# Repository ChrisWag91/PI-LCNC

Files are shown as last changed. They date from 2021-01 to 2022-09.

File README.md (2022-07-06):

 
# PI-LCNC

*THIS REPOSITORY IS WORK IN PROGRESS*

An open source project to use a Raspberry Pi 4 as a CNC controller using LinuxCNC.

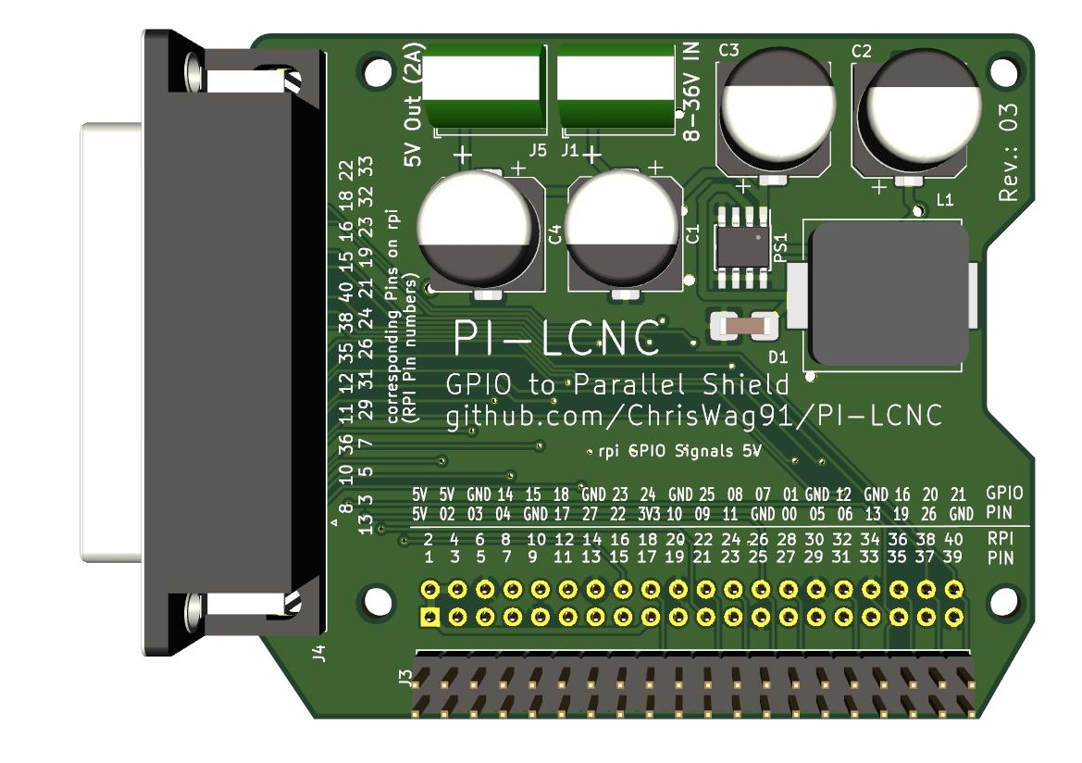
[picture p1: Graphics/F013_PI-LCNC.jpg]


You can find further information about the concept in this Youtube video:

<a href="https://youtu.be/qL530kJUmII
" target="_blank">Detailed Youtube Video</a>

It is designed to work combined with the [*RPI Levelshifter Hat*](https://github.com/ChrisWag91/rpi_level_shifter_hat) and a *CNC Breakout Board* with a parallel interface.

RPI 4 <==> [RPI Levelshifter Hat](https://github.com/ChrisWag91/rpi_level_shifter_hat) <==> PI-LCNC <==> [CNC-BOB (=Break out Board)](https://www.aliexpress.com/wholesale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)

*Concept:*

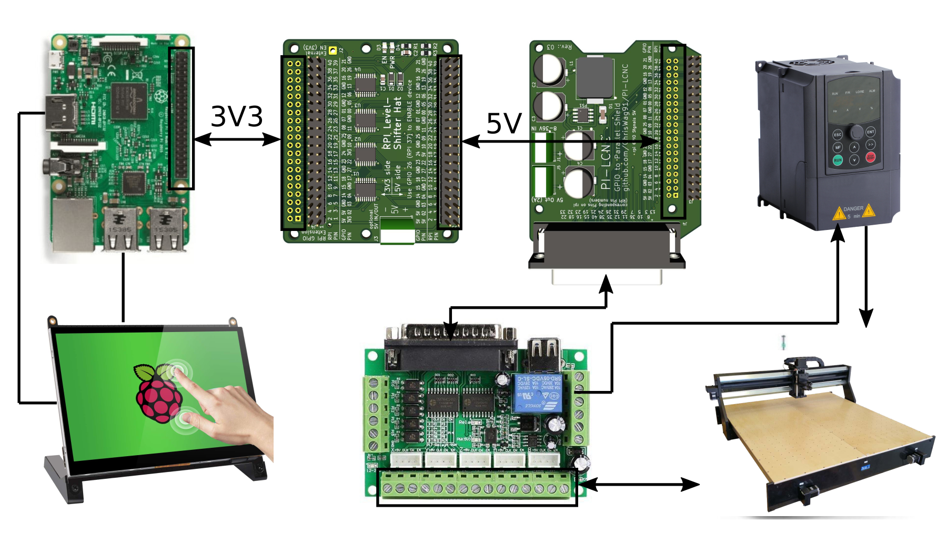
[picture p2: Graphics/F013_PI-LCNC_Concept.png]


This repository contains the manufacturing data for the PI-LCNC adapter PCB as well as configuration instructions and files for Linux CNC.

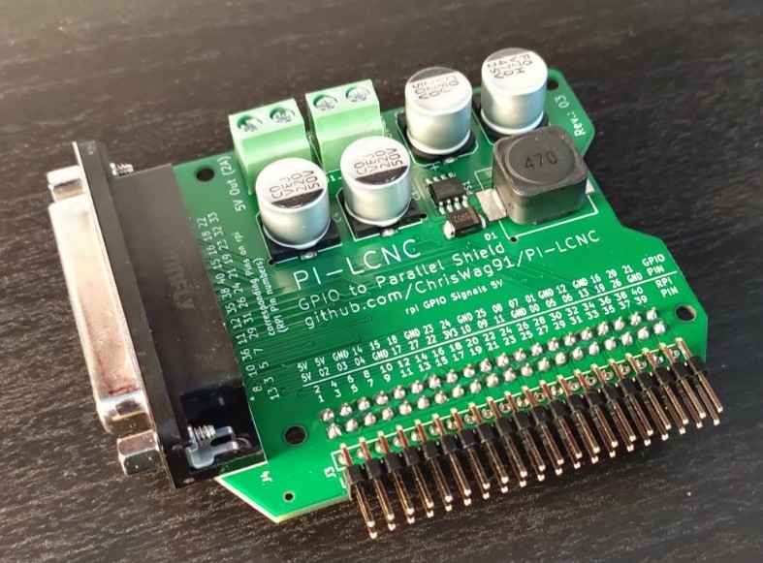
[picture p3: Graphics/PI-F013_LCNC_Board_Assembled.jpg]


Make sure to check the steps given under *Usage & Setup*

## Features
- DC-DC Power Supply for Raspberry Pi (Input Voltage 8-36V)
- Adapter for LPT connector
- Pin header for additional 5V signals from the Raspberry Pi

## Limitations
- 15000 Steps / s max due to Jitter of RPI

## Get PCB kits here:
Please contact me under chris@chris-design.at if you want to buy a kit containing the PCBs and the hardware.

## Required Hardware
- 1pcs  Raspberry Pi 4 (4GB or 8GB)
- 1pcs  [RPI Levelshifter Hat](https://github.com/ChrisWag91/rpi_level_shifter_hat)
- 2pcs  40 Pin Header Female (20x2 Pins)
- 2pcs  40 Pin Header Male (20x2 Pins) (optionally 1)
- 3pcs  screw Terminal P= 5mm (optional)
- 8pcs  M2.5 x 12mm Standoffs
- 4pcs  M2.5 x 5mm Screws
- optional mounting bracket

## Usage

### Electrical Setup
1. Solder up the RPI Levelshifter Hat as shown here: https://github.com/ChrisWag91/rpi_level_shifter_hat 
2. Solder up the PI-LCNC board as shown aboth
3. Remove the retaining standoffs from the LPT connector on the PI-LCNC board
4. Attach Raspberry Pi to RPI Levelshifter Hat using Standoffs
5. Attach PI-LCNC on top to RPI Levelshifter Hat as shown here:

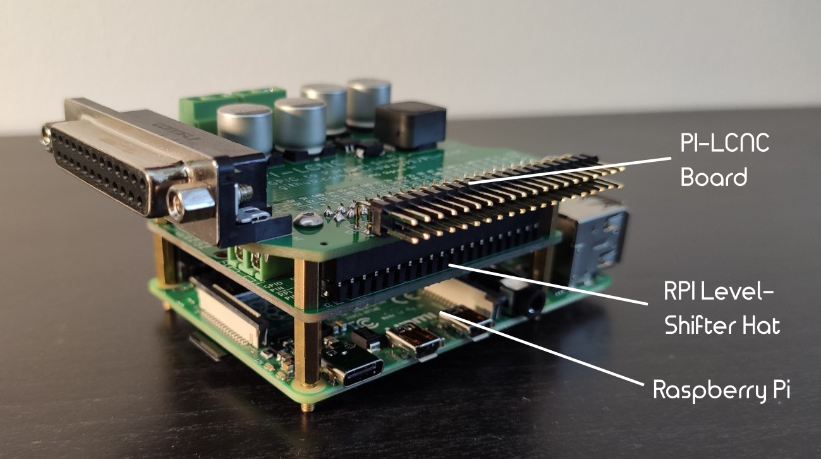
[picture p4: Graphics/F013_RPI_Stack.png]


**Attention** Don’t attach the PI-LCNC Board directly to your Raspberry - It will short the 3.3V and 5V rails.

6. Plug the CNC-BOB into the LPT Connector on the PI-LCNC Board
    
    Remove the studs on the female LPT Connector in order to fit the Connector of the BOB directly.
    Alternatively a LPT Extension cable can be used.

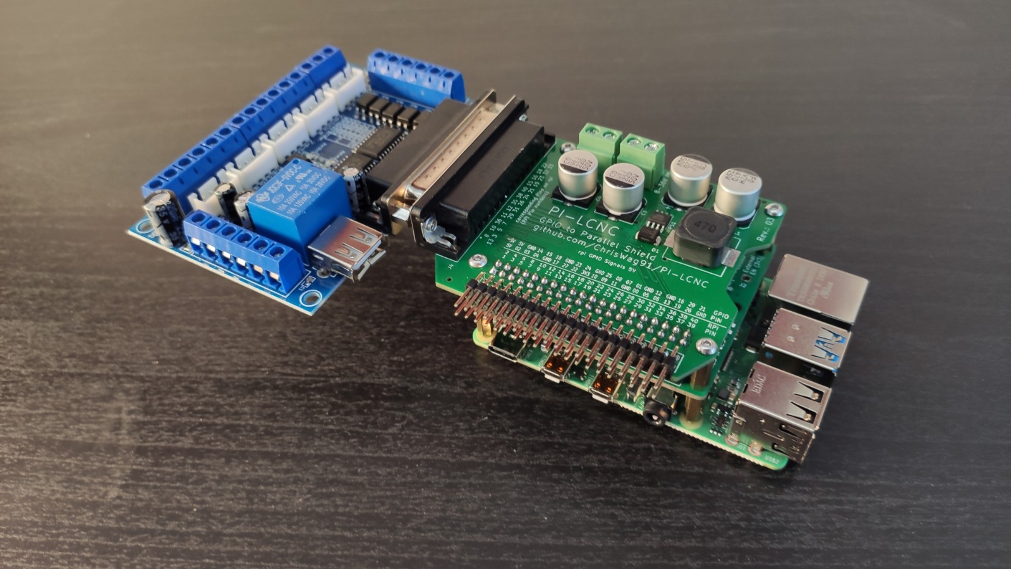
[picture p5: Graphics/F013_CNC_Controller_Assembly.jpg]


7. Wire the 5V output on PI-LCNC into the "PC5V" and "PCGND" on CNC-BOB
8. Wire the 8-36V input on PI-LCNC into the power supply of your machine

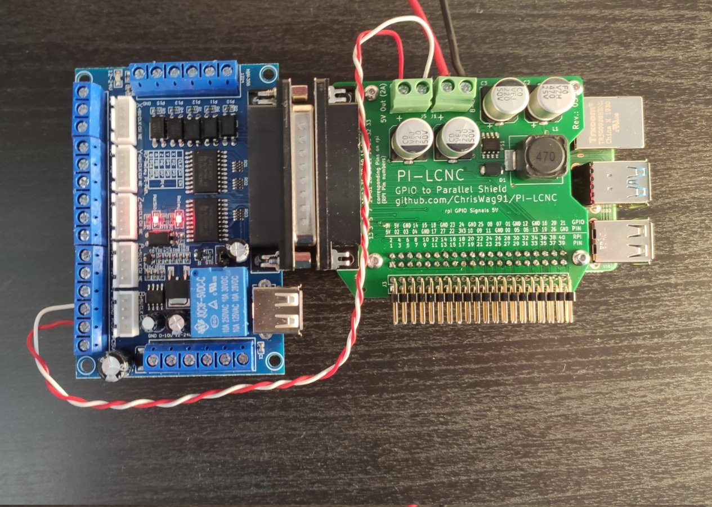
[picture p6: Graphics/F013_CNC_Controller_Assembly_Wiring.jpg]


9. Wire the CNC-BOB into your Machine

### Software Setup
#### The easy way

1. Download a prepared Raspberry Pi 4 Os from [here](https://drive.google.com/drive/folders/10dqpASeUx74fC9Wrch0KFPeILPTqw7Ok?usp=sharing).
This image has specific changes for the RPI-Levelshifter and for the PI-LCNC board already applied. It ships with a few 3 axis sample configurations for a cnc router.

2. Flash the image to an sd card
    * For Linux users: Write image to SD card using dd

    ```console
    sudo dd if=20XX-XX-XX-raspberry-pi_PI_LCNC.img of=/dev/sdx bs=1M status=progress
    ```

    * For Windows users: Write image to SD card using a tool like [Win32DiskImager](https://win32diskimager.org/)
3. After the first boot you should end up with a desktop like this (via vnc or display):

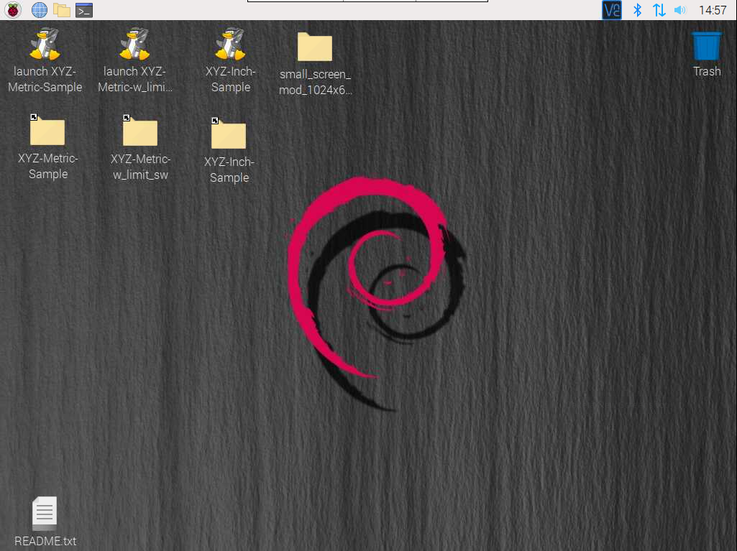
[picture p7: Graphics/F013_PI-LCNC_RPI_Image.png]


4. Make sure that the EN led on the RPI-Levelshifter is on

5. Choose a sample configuration as a starting point.
For example: "XYZ-Metric-Sample"

6. Modify the configuration file according to your CNC hardware. The configuration files can be found in one of the folders placed on the desktop:

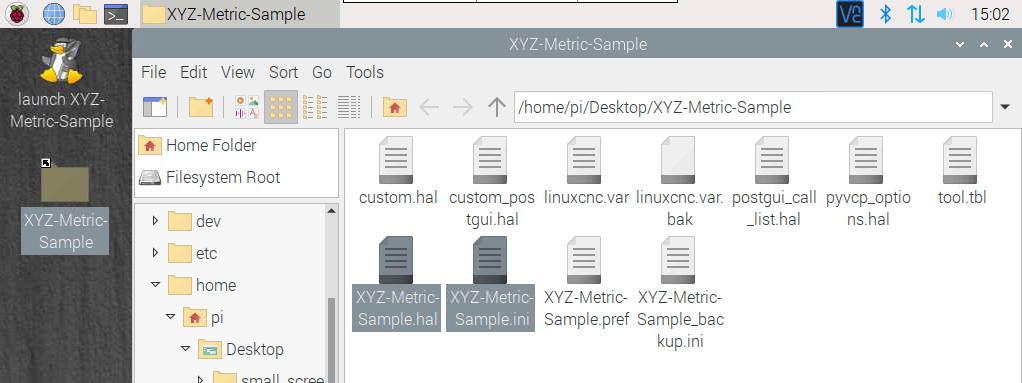
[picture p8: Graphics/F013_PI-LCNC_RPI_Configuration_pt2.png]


7. Change the **[Configuration Name].ini** file according to your setup. 

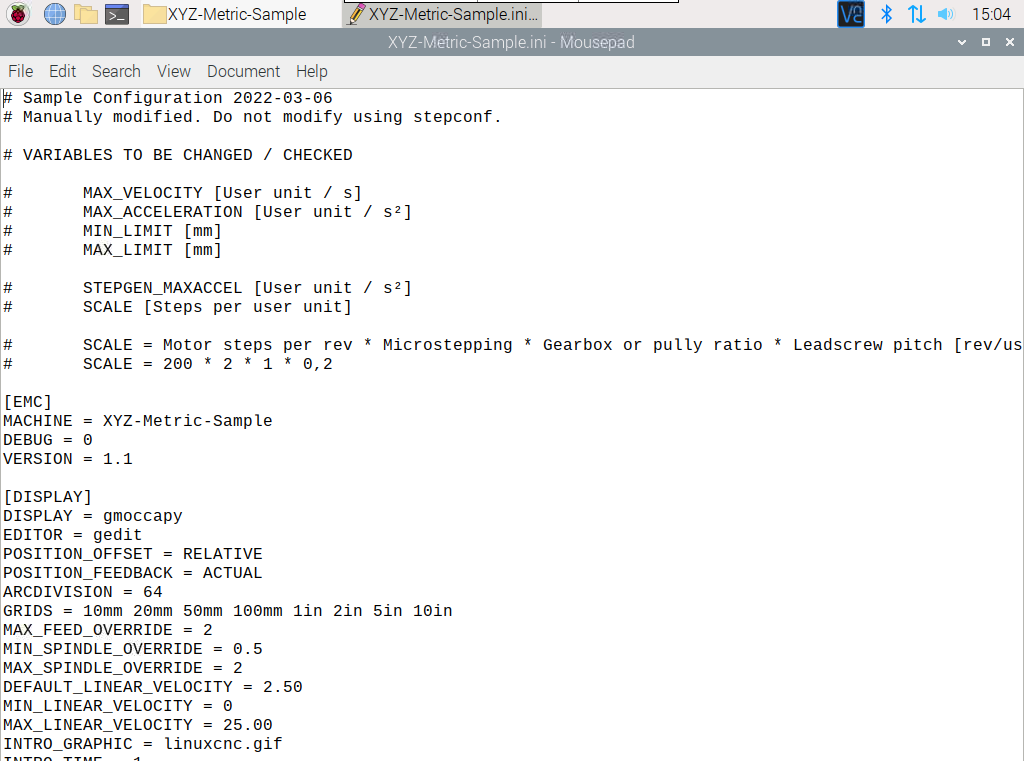
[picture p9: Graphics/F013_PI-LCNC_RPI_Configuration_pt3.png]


Modify at least these Variables for each of your machines axis:

-	MAX_VELOCITY [User unit / s]
-	MAX_ACCELERATION [User unit / s²]
-	MIN_LIMIT [mm]
-	MAX_LIMIT [mm]

-	STEPGEN_MAXACCEL [User unit / s²]
-	SCALE [Steps per user unit]

-	SCALE = Motor steps per rev * Microstepping * Gearbox or pully ratio * Leadscrew pitch [rev/user unit]
-	SCALE = 200 * 2 * 1 * 0,2 (EXAMPLE)

This should make your machine move properly if you start the corresponding sample CNC interface.

8. [OPTIONAL] If you need to make changes to the pinout of the CNC controller, edit the **[Configuration Name].hal** file according to your needs.

#### The hard way
1. Flash realtime capable version of Raspberry Os onto an sd card.
You can download a precompiled RT-Raspberry Os with Linux CNC already pre installed from this link: 
http://www.linuxcnc.org/iso/
(use one of the -pi4 variants, tested with 2.8.0)

2. Now we need to automatically enable the RPI Level Shifter Hat on boot: 

    Copy the script "enable_rpi_logic_level_shifter.py" from [here](https://github.com/ChrisWag91/rpi_level_shifter_hat/tree/master/Examples) to a local directory on your raspberry and add it to the autostart file as follows:

    ```console	
    sudo nano /etc/rc.local
    ```

    Add the following line before "exit 0":

    ```console	
    python /[insert local path to the enable script]/enable_rpi_logic_level_shifter.py &
    ```

2. Generate a new machine configuration according to your hardware using the Stepconf wizard

    Make sure to choose **Use Gmoccapy Screen** in the tab Options
    This configuration will not start out of the Box, because it expects the parport hardware to be present.
    It should run as soon as the next step is done.

3. Change the pinout according to the [example hal and ini file](https://github.com/ChrisWag91/PI-LCNC/tree/master/Linux%20CNC%20configuration%20files) found in this repository.

    I would advise to copy the files from this repo and change the machine parameters to fit your machine.
    The files need to be named to [Name of your machine].ini and [Name of your machine].hal.
    All references to "my-mill" in [Name of your machine].ini need to be changed to [Name of your machine].
    Make sure to backup the automatically generated files before replacing them, since you can copy the machine parameters from there to the new files.

4. Launch Linux-CNC

    You should end up with something like that:

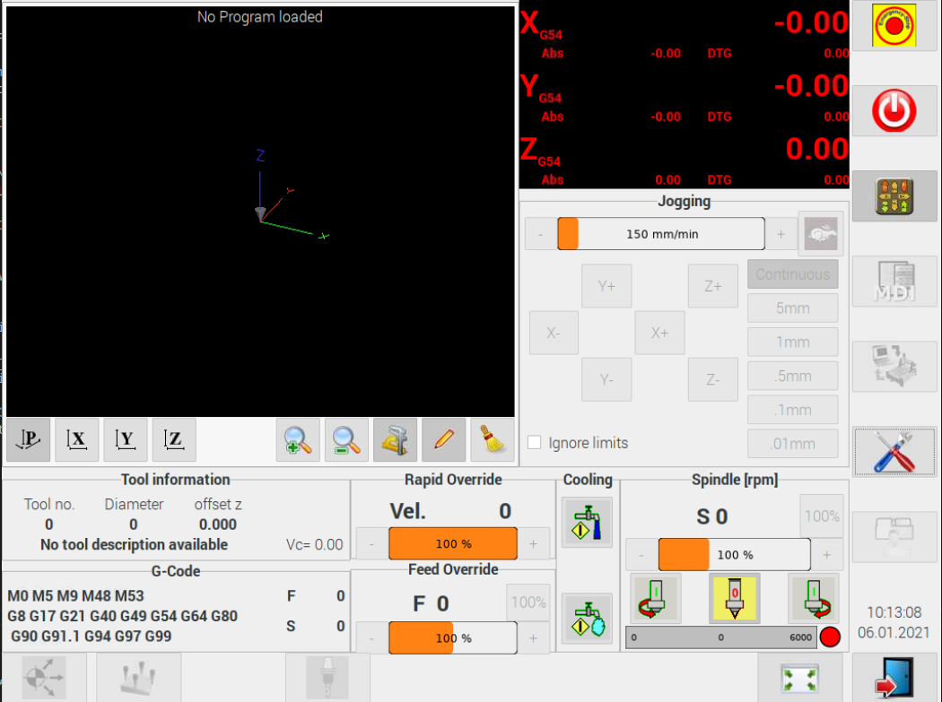
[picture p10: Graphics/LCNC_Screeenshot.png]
    

*******************************************************************************************************************************

## Warning
This design is distributed in the hope that it will be useful, but WITHOUT ANY WARRANTY. Without even the implied warranty of MERCHANTABILITY or FITNESS FOR A PARTICULAR PURPOSE. See the GNU General Public License for more details.

## License
<a href="https://mirrors.creativecommons.org/presskit/buttons/88x31/png/by-nc.png
" target="_blank"></a>

License text: 
https://creativecommons.org/licenses/by-nc/3.0/

*******************************************************************************************************************************

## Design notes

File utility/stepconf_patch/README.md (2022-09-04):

#  Patch for Stepconf for easy configuration of PI-LCNC Board

## THIS IS WORK IN PROGRESS

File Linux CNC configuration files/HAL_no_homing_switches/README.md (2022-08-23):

# HAL Configuration for common chinese breakout board

This HAL file is configured to work with boards like shown below:

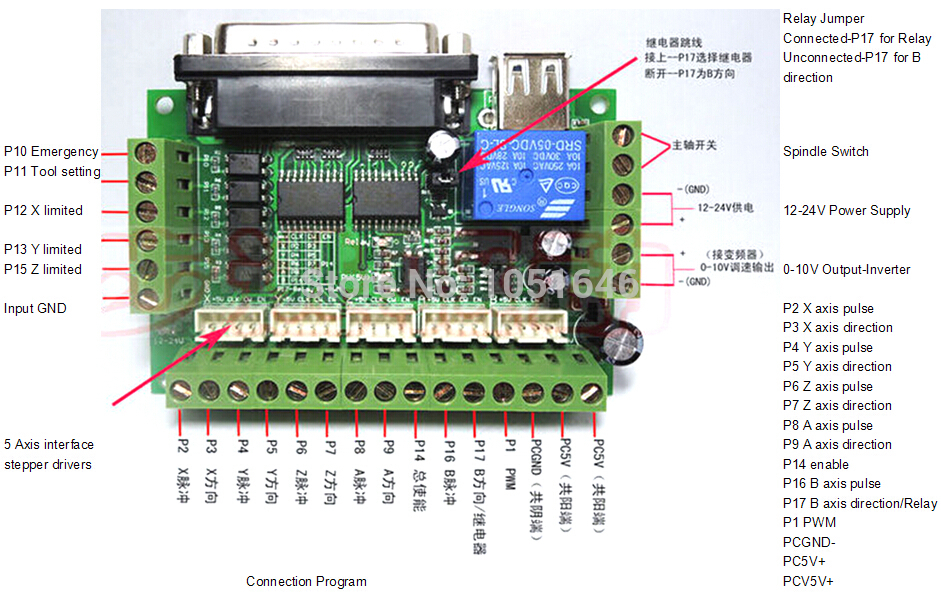
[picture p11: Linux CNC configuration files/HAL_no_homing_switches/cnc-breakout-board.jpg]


Adaptation of these files according to the machine configuration will be necessary. This is just a starting point.

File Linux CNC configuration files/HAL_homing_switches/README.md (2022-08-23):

# HAL Configuration for common chinese breakout board

This HAL file is configured to work with boards like shown below:



Adaptation of these files according to the machine configuration will be necessary. This is just a starting point.

# Homing / Limit Switches

If you use the optocouplers on the breakout board (P12-P15) for limit / homing switches you need to add pullup resistors to the corresponding channels as shown below. The resistors can be added on the extension header of the PI-LCNC board.

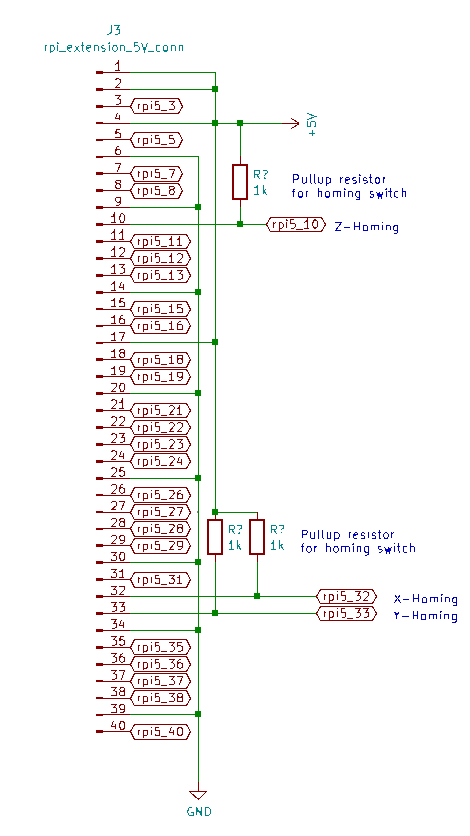
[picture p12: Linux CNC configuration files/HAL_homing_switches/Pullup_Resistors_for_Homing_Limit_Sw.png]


Alternatively you can use the pins on the GPIO extension header directly for limit switches.

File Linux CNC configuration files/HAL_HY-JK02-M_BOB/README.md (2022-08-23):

# HAL Configuration for Chinese HY-JK02-M Breakout board

This HAL file is configured to work with boards like shown below:

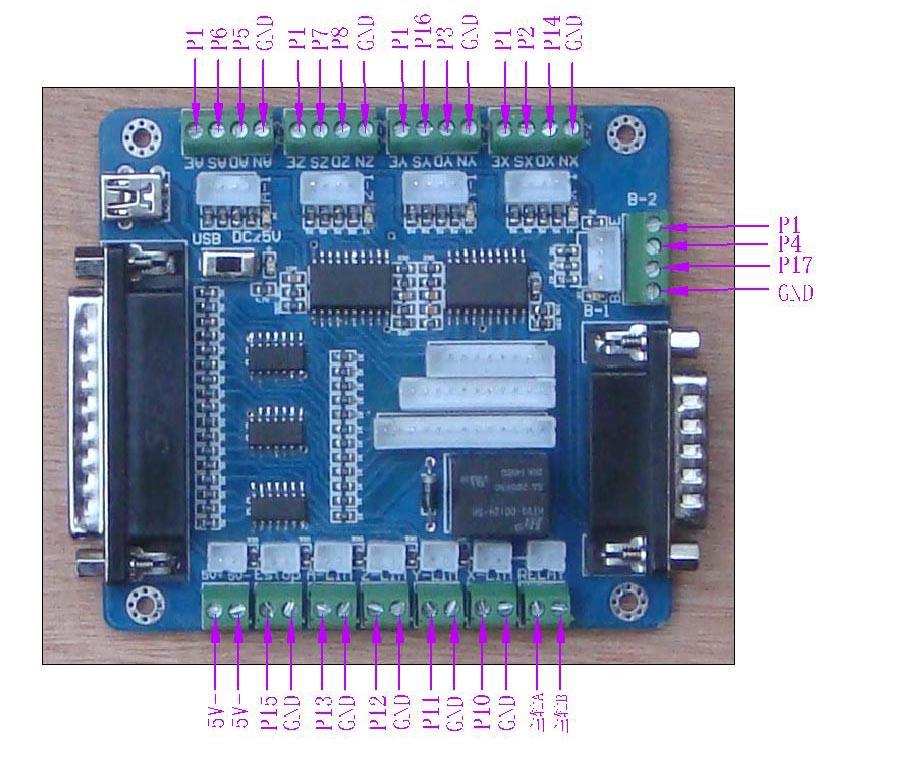
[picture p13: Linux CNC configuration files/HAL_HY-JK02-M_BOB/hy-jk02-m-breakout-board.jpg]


Adaptation of these files according to the machine configuration will be necessary. This is just a starting point.

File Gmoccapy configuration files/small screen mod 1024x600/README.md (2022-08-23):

# Gmoccapy modification for 1024x600 touch screen

THIS PROJECT IS WORK IN PROGRESS.
USE AT YOUR OWN RISK.

This folder contains modified UI files in order to run Gmoccapy with a small touch screen.

## Installation
- Set the resolution (only needed if not automatically detected):
    edit /boot/config.txt:
    
    ```console
    sudo nano /boot/config.txt
    ```
    change / add the following lines in the file:

    ```console
    hdmi_cvt=1024 600 60 6
    hdmi_group=2
    hdmi_mode=87
    hdmi_drive=2
    ```
- Copy the content of this folder to your Raspberry
- Execute deploy_tiny_gmoccapy.sh
    ```console
    cd /[Path to the folder you copied the files to]
    sudo chmod +x deploy_tiny_gmoccapy.sh
    sudo ./deploy_tiny_gmoccapy.sh
    ```
- You may need to change the DRO size parameter under "Settings - DRO - Size"

Result:

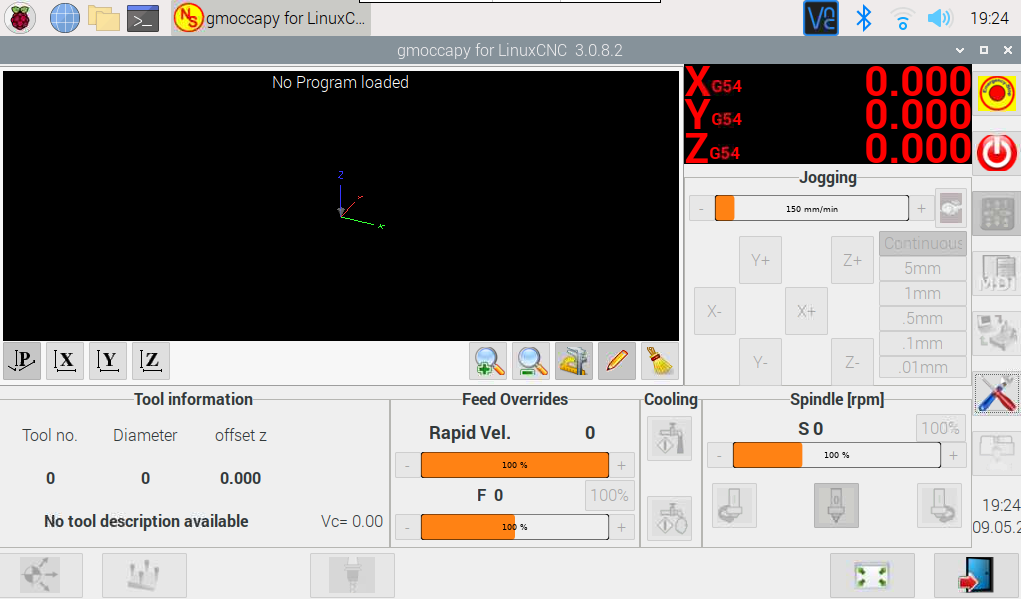
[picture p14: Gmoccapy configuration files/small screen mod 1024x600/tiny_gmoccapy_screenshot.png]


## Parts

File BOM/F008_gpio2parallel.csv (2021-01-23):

Comment | Designator | Footprint | LCSC | LCSC_ALT
470uF | C2 | Capacitor_SMD:CP_Elec_10x10 | C249933 | C3350
220uF | C3,C1,C4 | Capacitor_SMD:CP_Elec_10x10 | C176670
D_SS52 | D1 | SS52BF:SS34 | C51497
Power_In_8-36 | J1 | TerminalBlock_RND:TerminalBlock_RND_205-00045_1x02_P5.00mm_Horizontal
rpi_5V_conn | J2 | Connector_PinHeader_2.54mm:PinHeader_2x20_P2.54mm_Vertical
rpi_extension_5V_conn | J3 | Connector_PinHeader_2.54mm:PinHeader_2x20_P2.54mm_Vertical | C97262
DB25_Female | J4 | Connector_Dsub:DSUB-25_Female_Horizontal_P2.77x2.84mm_EdgePinOffset7.70mm_Housed_MountingHolesOffset9.12mm | C77838
Power_Out_5 | J5 | TerminalBlock_RND:TerminalBlock_RND_205-00045_1x02_P5.00mm_Horizontal
47uH | L1 | L_costum:L_14x13mm_H6mm | C169376 | C163686, C182149
TD1509P5 | PS1 | Package_SO:PowerIntegrations_SO-8 | C97262

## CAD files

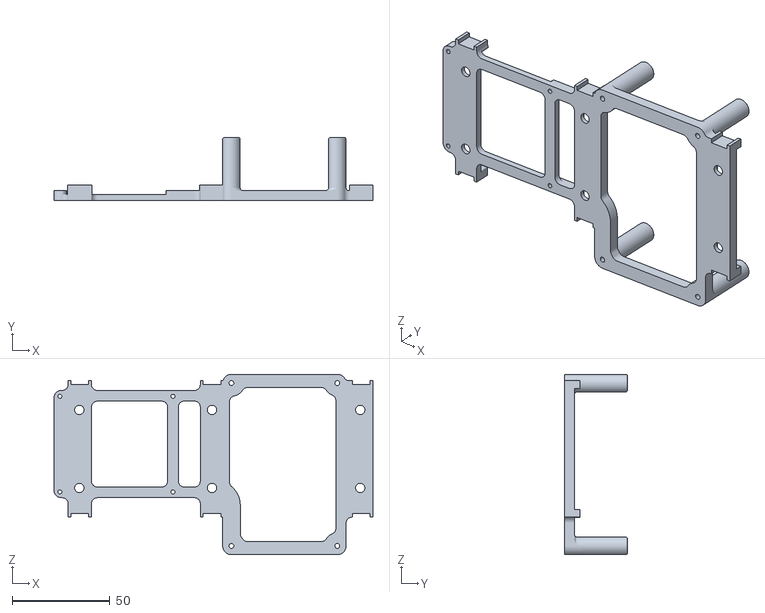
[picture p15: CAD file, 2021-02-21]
CAD/F013_Carrier_001.stl
163.5 x 32.2 x 92.5

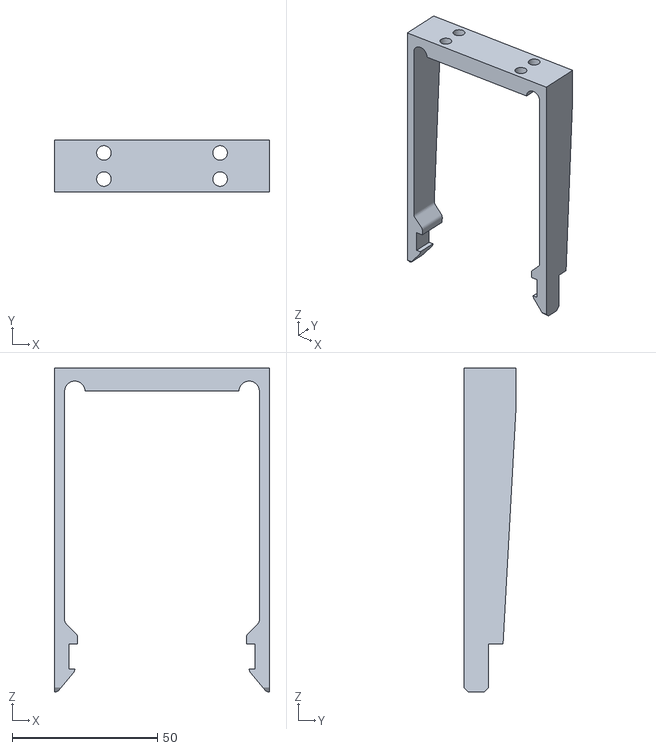
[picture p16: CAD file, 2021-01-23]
CAD/F013_Carrier_Clip_Long.stl
74.0 x 18.0 x 111.5

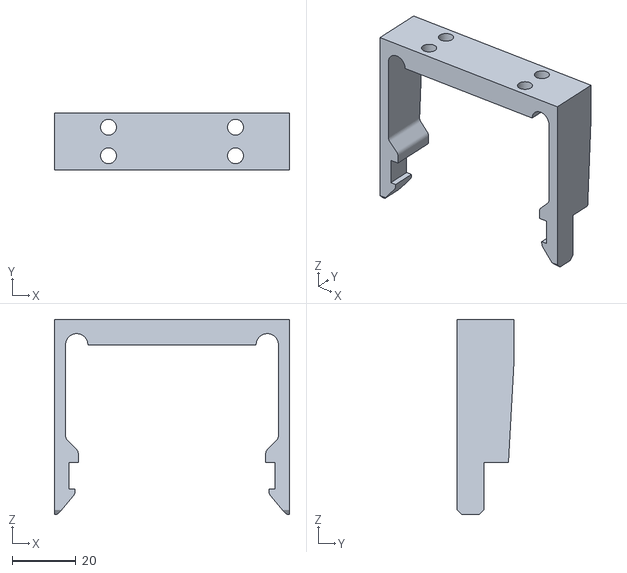
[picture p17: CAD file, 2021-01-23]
CAD/F013_Carrier_Clip_Short.stl
74.0 x 18.0 x 61.5

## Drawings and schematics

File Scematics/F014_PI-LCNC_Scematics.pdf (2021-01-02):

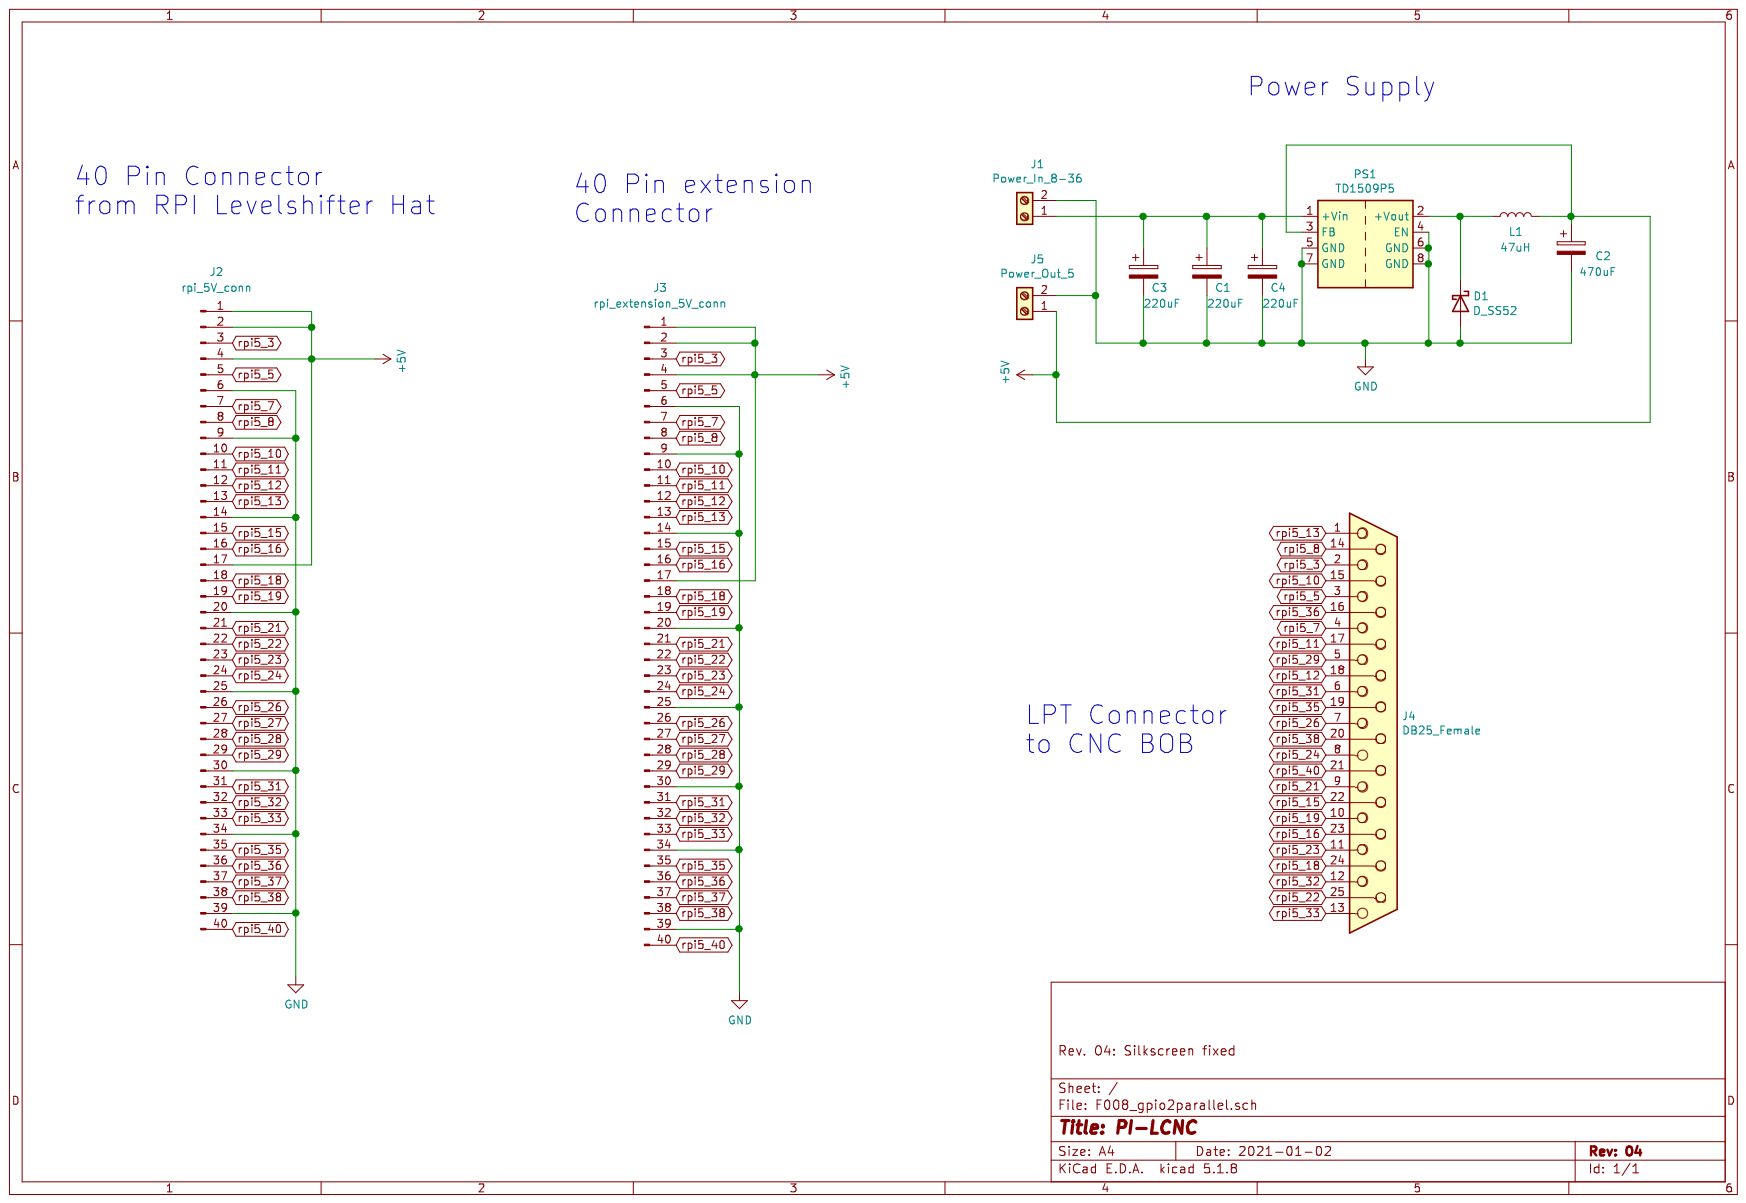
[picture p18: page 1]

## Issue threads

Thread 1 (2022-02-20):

Ref GND to ParPort signals

Adamantan, 2022-02-20:
Hi Chris,

Thank you for sharing your designs!
Going through the design files after I have encountered some electrical issues during integration, I have noticed that there is no GND line in the 25 pin D-SUB connector.
What is the intended return current path for these signals?
Thank you for your explanation in advance!

Kind regards,
Adam

ChrisWag91, 2022-02-23:
Hi Adam,
I designed the board for a specific BOB which is supplied with power (and therefore a ground) by the 5V out on the board.
I also needed a few more 5V signals spilced out form the connector than the standard for D-SUB would allow for.
But adding a few ground pins for the cost of a few signals might make sense in a future revision.

cheers,
chris

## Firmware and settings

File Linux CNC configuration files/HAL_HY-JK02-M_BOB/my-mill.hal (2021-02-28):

# Generated by stepconf 1.1 at Sat Feb 15 17:11:34 2020
# If you make changes to this file, they will be
# overwritten when you run stepconf again
# loadrt trivkins
loadrt [KINS]KINEMATICS
loadrt [EMCMOT]EMCMOT base_period_nsec=[EMCMOT]BASE_PERIOD servo_period_nsec=[EMCMOT]SERVO_PERIOD num_joints=[KINS]JOINTS
loadrt pwmgen output_type=0,0

loadrt charge_pump

# gpio pins:
# 2 2 2 2 2 2 2 2 1 1 1 1 1 1 1 1 1 1
# 7 6 5 4 3 2 1 0 9 8 7 6 5 4 3 2 1 0 9 8 7 6 5 4 3 2 (gpio0 not used )
# rpi pins:
# 1 3 2 1 1 1 4 3 3 1 1 3 1   3 3 2 1 2 2 2 3 2      
# 3 7 2 8 6 5 0 8 5 2 1 6 0 8 3 2 3 9 1 4 6 1 9 7 5 3
# serial connector pins with GPIO to Parallel Shield:
#     2 2 2 2 2 2 1 1 1 1 1 1 1 1 1 1 
# 1   5 4 3 2 1 0 9 8 7 6 5 4 3 2 1 0 9 8 7 6 5 4 3 2
#
# 1 0 0 0 0 0 0 0 0 0 1 1 1 1 0 0 0 0 1 1 1 1 1 1 1 1 dir     mask (0 means in   1 means out)      dec 33616127
# 0 1 1 1 1 1 1 1 1 1 0 0 0 0 0 0 0 0 0 0 0 0 0 0 0 0 exclude mask (0 means use  1 means dont use) dec 33488896

loadrt hal_pi_gpio dir=33616127 exclude=33488896

loadrt stepgen step_type=0,0,0

addf stepgen.make-pulses base-thread
loadrt sum2 count=1
loadrt not count=1

addf stepgen.capture-position servo-thread
addf motion-command-handler servo-thread
addf motion-controller servo-thread
addf stepgen.update-freq servo-thread
addf hal_pi_gpio.read  base-thread
addf hal_pi_gpio.write base-thread

addf pwmgen.update servo-thread
addf pwmgen.make-pulses base-thread

##################################################################
#           Spindle Outputs
##################################################################

#net spindle-cmd-rpm     <= spindle.0.speed-out
#net spindle-cmd-rpm-abs <= spindle.0.speed-out-abs
net spindle-cmd-rps     <= spindle.0.speed-out-rps
net spindle-cmd-rps-abs <= spindle.0.speed-out-rps-abs
net spindle-at-speed    => spindle.0.at-speed

net spindle-speed-cmd spindle.0.speed-out => pwmgen.0.value
net spindle-on spindle.0.on => pwmgen.0.enable
net spindle-on => hal_pi_gpio.pin-11-out
# Set the spindle's top speed in RPM
setp pwmgen.0.scale -24000
setp pwmgen.0.offset 1.05

####################d##############################################
#           Laser Outputs
###################################################################

net laser-pwr spindle.0.speed-out-abs => pwmgen.1.value
setp pwmgen.1.enable 1
setp pwmgen.1.scale 100

#setp pwmgen.1.pwm-freq 2000
#setp pwmgen.1.offset 0
setp pwmgen.1.dither-pwm true

#net laser-pwm pwmgen.1.pwm => hal_pi_gpio.pin-36-out

##################################################################
#           Stepper Outputs
##################################################################

#Attention - Pin Numbers are RPI Numbers not GPIO Numbers
net xenable		=> hal_pi_gpio.pin-13-out
net xstep		=> hal_pi_gpio.pin-03-out
net xdir		=> hal_pi_gpio.pin-08-out
net ystep		=> hal_pi_gpio.pin-36-out
net ydir		=> hal_pi_gpio.pin-05-out
net zstep		=> hal_pi_gpio.pin-26-out
net zdir		=> hal_pi_gpio.pin-24-out
net astep		=> hal_pi_gpio.pin-31-out
net adir		=> hal_pi_gpio.pin-29-out
#net bstep		=> hal_pi_gpio.pin-07-out
#net bdir		=> hal_pi_gpio.pin-11-out

##################################################################
#           General Outputs
##################################################################
#net coolant iocontrol.0.coolant-flood		=> hal_pi_gpio.pin-10-out

##################################################################
#           Homing Inputs
##################################################################
#net min-home-x     <=  hal_pi_gpio.pin-19-in
#net min-home-y     <=  hal_pi_gpio.pin-23-in
#net min-home-z     <=  hal_pi_gpio.pin-32-in

#net min-home-x => joint.0.home-sw-in
#net min-home-y => joint.1.home-sw-in
#net min-home-z => joint.2.home-sw-in

setp stepgen.0.position-scale [JOINT_0]SCALE
setp stepgen.0.steplen 1
setp stepgen.0.stepspace 0
setp stepgen.0.dirhold 26500
setp stepgen.0.dirsetup 26500
setp stepgen.0.maxaccel [JOINT_0]STEPGEN_MAXACCEL
net xpos-cmd joint.0.motor-pos-cmd => stepgen.0.position-cmd
net xpos-fb stepgen.0.position-fb => joint.0.motor-pos-fb
net xstep <= stepgen.0.step
net xdir <= stepgen.0.dir
net xenable joint.0.amp-enable-out => stepgen.0.enable

setp stepgen.1.position-scale [JOINT_1]SCALE
setp stepgen.1.steplen 1
setp stepgen.1.stepspace 0
setp stepgen.1.dirhold 26500
setp stepgen.1.dirsetup 26500
setp stepgen.1.maxaccel [JOINT_1]STEPGEN_MAXACCEL
net ypos-cmd joint.1.motor-pos-cmd => stepgen.1.position-cmd
net ypos-fb stepgen.1.position-fb => joint.1.motor-pos-fb
net ystep <= stepgen.1.step
net ydir <= stepgen.1.dir
net yenable joint.1.amp-enable-out => stepgen.1.enable

setp stepgen.2.position-scale [JOINT_2]SCALE
setp stepgen.2.steplen 1
setp stepgen.2.stepspace 0
setp stepgen.2.dirhold 26500
setp stepgen.2.dirsetup 26500
setp stepgen.2.maxaccel [JOINT_2]STEPGEN_MAXACCEL
net zpos-cmd joint.2.motor-pos-cmd => stepgen.2.position-cmd
net zpos-fb stepgen.2.position-fb => joint.2.motor-pos-fb
net zstep <= stepgen.2.step
net zdir <= stepgen.2.dir
net zenable joint.2.amp-enable-out => stepgen.2.enable

net estop-out <= iocontrol.0.user-enable-out
net estop-out => iocontrol.0.emc-enable-in

loadusr -W hal_manualtoolchange
net tool-change iocontrol.0.tool-change => hal_manualtoolchange.change
net tool-changed iocontrol.0.tool-changed <= hal_manualtoolchange.changed
net tool-number iocontrol.0.tool-prep-number => hal_manualtoolchange.number
net tool-prepare-loopback iocontrol.0.tool-prepare => iocontrol.0.tool-prepared

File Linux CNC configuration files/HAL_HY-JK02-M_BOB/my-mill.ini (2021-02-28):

# Generated by stepconf 1.1 at Sat Feb 15 17:11:34 2020
# If you make changes to this file, they will be
# overwritten when you run stepconf again

[EMC]
MACHINE = my-mill
DEBUG = 0
VERSION = 1.1

[DISPLAY]
DISPLAY = gmoccapy
EDITOR = gedit
POSITION_OFFSET = RELATIVE
POSITION_FEEDBACK = ACTUAL
ARCDIVISION = 64
GRIDS = 10mm 20mm 50mm 100mm 1in 2in 5in 10in
MAX_FEED_OVERRIDE = 2
MIN_SPINDLE_OVERRIDE = 0.5
MAX_SPINDLE_OVERRIDE = 2
DEFAULT_LINEAR_VELOCITY = 2.50
MIN_LINEAR_VELOCITY = 0
MAX_LINEAR_VELOCITY = 25.00
INTRO_GRAPHIC = linuxcnc.gif
INTRO_TIME = 1
PROGRAM_PREFIX = /home/pi/linuxcnc/nc_files
INCREMENTS = 5mm 1mm .5mm .1mm .01mm

[KINS]
JOINTS = 3
KINEMATICS = trivkins coordinates=XYZ

[FILTER]
PROGRAM_EXTENSION = .png,.gif,.jpg Greyscale Depth Image
PROGRAM_EXTENSION = .py Python Script
PROGRAM_EXTENSION = .nc,.tap G-Code File
png = image-to-gcode
gif = image-to-gcode
jpg = image-to-gcode
py = python

[TASK]
TASK = milltask
CYCLE_TIME = 0.010

[RS274NGC]
PARAMETER_FILE = linuxcnc.var

[EMCMOT]
EMCMOT = motmod
COMM_TIMEOUT = 1.0
BASE_PERIOD = 100000
SERVO_PERIOD = 1000000

[HAL]
HALUI = halui
HALFILE = my-mill.hal
HALFILE = custom.hal
POSTGUI_HALFILE = postgui_call_list.hal

[HALUI]
# add halui MDI commands here (max 64) 

[TRAJ]
COORDINATES =  X Y Z
LINEAR_UNITS = mm
ANGULAR_UNITS = degree
DEFAULT_LINEAR_VELOCITY = 2.50
MAX_LINEAR_VELOCITY = 25.00

[EMCIO]
EMCIO = io
CYCLE_TIME = 0.100
TOOL_TABLE = tool.tbl

[AXIS_X]
MAX_VELOCITY = 25.0
MAX_ACCELERATION = 750.0
MIN_LIMIT = -1000
MAX_LIMIT = 1000

[JOINT_0]
TYPE = LINEAR
HOME = 0.0
MIN_LIMIT = -1000
MAX_LIMIT = 1000
MAX_VELOCITY = 25.0
MAX_ACCELERATION = 750.0
STEPGEN_MAXACCEL = 937.5
SCALE = -80.0
FERROR = 1
MIN_FERROR = .25
# Homing switch in neg. dir
#HOME_OFFSET = 0.0
#HOME_SEARCH_VEL = 15.00000		
#Sign defines direction; Value defines speed; ATTENTION: Velocity for METRIC setup. Reduce significantly if you use Imperial units
#HOME_LATCH_VEL = -1.00000		
#Final homing speed; Sign defines direction
#HOME_SEQUENCE = 1				
#Defines homing order for "HOME ALL"

[AXIS_Y]
MAX_VELOCITY = 25.0
MAX_ACCELERATION = 750.0
MIN_LIMIT = -1000
MAX_LIMIT = 1000

[JOINT_1]
TYPE = LINEAR
HOME = 0.0
MIN_LIMIT = -1000
MAX_LIMIT = 1000
MAX_VELOCITY = 25.0
MAX_ACCELERATION = 750.0
STEPGEN_MAXACCEL = 937.5
SCALE = -80.0
FERROR = 1
MIN_FERROR = .25
# Homing switch in neg. dir
#HOME_OFFSET = 0.000000
#HOME_SEARCH_VEL = 15.00000		
#Sign defines direction; Value defines speed; ATTENTION: Velocity for METRIC setup. Reduce significantly if you use Imperial units
#HOME_LATCH_VEL = 1.00000		
#Final homing speed; Sign defines direction
#HOME_SEQUENCE = 1				
#Defines homing order for "HOME ALL"

[AXIS_Z]
MAX_VELOCITY = 25.0
MAX_ACCELERATION = 750.0
MIN_LIMIT = -100.0
MAX_LIMIT = 100

[JOINT_2]
TYPE = LINEAR
HOME = 0.0
MIN_LIMIT = -100.0
MAX_LIMIT = 100
MAX_VELOCITY = 25.0
MAX_ACCELERATION = 750.0
STEPGEN_MAXACCEL = 937.5
SCALE = 80.0
FERROR = 1
MIN_FERROR = .25
# Homing switch in neg. dir
#HOME_OFFSET = 0.000000
#HOME_SEARCH_VEL = -15.00000		
#Sign defines direction; Value defines speed; ATTENTION: Velocity for METRIC setup. Reduce significantly if you use Imperial units
#HOME_LATCH_VEL = -1.00000		
#Final homing speed; Sign defines direction
#HOME_SEQUENCE = 1				
#Defines homing order for "HOME ALL"

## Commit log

2021-01-23 CAD files added
    [F008_gpio2parallel.csv, F013_Carrier.stl, F013_Carrier_Clip_Long.stl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]
2021-01-31 limit switch example added
    [my-mill.hal]
2021-02-21 Carrier improved
    [F013_Carrier.stl, F013_Carrier_001.stl]
2021-02-28 Documentation for additional BOBs
    [my-mill.hal]
2022-03-06 sample configurations added
    [XYZ-Inch-Sample.hal, XYZ-Metric-Sample.hal, XYZ-Metric-w_limit_sw.hal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]
